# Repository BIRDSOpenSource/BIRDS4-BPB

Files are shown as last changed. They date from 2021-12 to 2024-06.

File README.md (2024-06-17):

<div align="center">
  <a href="https://lean-sat.org/opensource/">
  
  </a>
</div>

 

# BIRDS4-BPB
 Documentation for the Backplane Board used in the BIRDS4 Satellite

## About the BIRDS4 Program:

The Mission Statement of the Project is:

> “By successfully building and operating first satellite of nation, advance toward indigenous space program in each country”

The project is led by Kyushu Institute of Technology in Japan and involves students from Philippines, Paraguay, Nepal, Turkey and Japan.

Satellite Names: Tsuru (Japan), Guarani-1 (Paraguay) and Maya-2 (Phillipines)

Stakeholders:  Paraguayan Space Agency, Polytechnic Faculty of National University of Asuncion, and Kyushu Institute of Technology (Kyutech) for Japan.

Project duration: 2018-2022

CubeSat: 1U (10x10x10) cm3

Weight: 1.13kg

Launch Date: 21st February 2021 

BIRDS-4 has 1 main missions in total; APRS Store and forward mission

## Organisation structure

```bash

├── .gitattributes
├── B4_BPB_FM_PartsList_PBan_20191024.xls
├── BPB_v16.brd
├── BPB_v16.pdf
├── BPB_v16.sch
├── BPB_v16_BOT.png
├── BPB_v16_TOP.png
├── LICENSE
├── Photo.png
└── README.md

```

> [!CAUTION]
> The files `.sch` and `.brd` files in this repositiry were created using Eagle software.
 
For those that want to import these files into 
KiCAD7 [here's how you do it](https://community.element14.com/technologies/open-source-hardware/b/blog/posts/working-with-kicad-7-importing-eagle-files) 
 or KiCAD5.1 [here's how you do it](https://www.youtube.com/watch?v=RBc02MwpKxk&t=1s).
## Features

## I like this project, can I help you?
You are welcome 🙂

* Give us a star ⭐
* Watch repository to be notified about updates 👀
* If you will find some errors, report them in Issues 🐞
* Try Birds designs on some real computer and let us know how it worked in Discussions. 💬
* We would greatly appreciate if you would also tell others about this ecosystem, it helps us to improve BIRDS Open Source. Thank you!

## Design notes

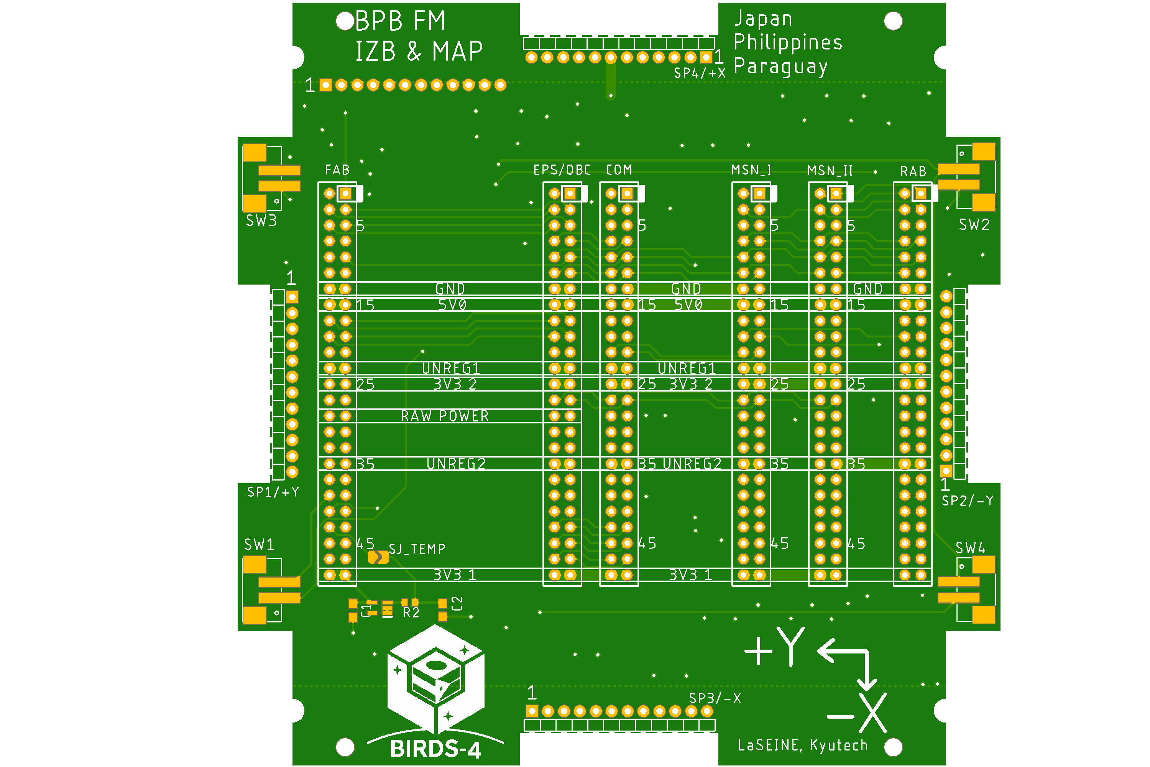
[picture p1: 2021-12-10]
BPB_v16_TOP.png

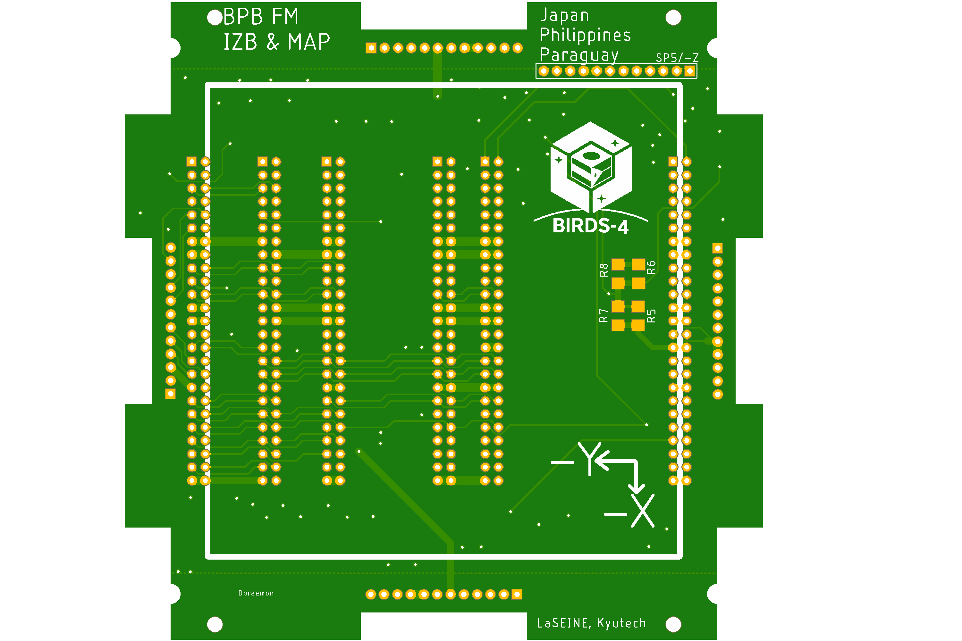
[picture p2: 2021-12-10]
BPB_v16_BOT.png

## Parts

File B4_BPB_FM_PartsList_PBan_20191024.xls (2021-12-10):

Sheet: 必ずお読みください
入力項目説明
メ ー カ ー |  |  | 電子部品のメーカー名をご入力ください。
部 品 種 別 |  |  | 電子部品の種別をご入力ください。例：チップ抵抗、トランジスタ、LED、など
電 子 部 品 型 番 |  |  | 電子部品の型番をご入力ください。 ※誤表記による不具合を回避するためにも正確なご入力をお願い致します。 ※表面実装の抵抗やコンデンサ(電解、タンタル以外)は、後述「電子部品見取り表」をご参照のうえ、ご入力ください。
配 置 記 号 / リファレンス |  |  | シルク図/配置図に表記された配置記号/リファレンス番号をご入力ください。 ※複数入力する場合は、カンマ「,」区切りでのご入力をお願い致します。 (入力例)R1～R5、R1-5と略さず、R1,R2,R3,R4,R5とご入力ください。 ※電子部品型番ベースでのご記入をお願い致します。（１つの電子部品型番に対して、配置番号を複数記入）
個 数 |  |  | 電子部品の個数をご入力ください。
ピ ン 数 |  |  | 電子部品の総ピン数をご入力ください。 ※基板取付穴、部品取付穴、全てのスルー・ノンスルーホール、面実装部品のパッド、及び次の①～⑤の配線を伴う箇所（①テストピン、②チェックランド、③引き出しランド、④ジャンパピン、⑤入出力ランドの総計。
実装 / 未実装 |  |  | 実装サービスでの「実装」/「未実装」をご選択ください。 ※同じ電子部品型番の中で実装と未実装が分かれる場合は、それぞれ2行に分けて配置記号をご入力ください。
部品分類 | SMD |  | 表面実装部品
 | DIP |  | 挿入部品
 | 特殊 BGA等 |  | BGA/CSP/LGA/QFNなど部品極性が部品の真下に配置された部品 -BGA：Ball Grid Array/下面に半田ボールの端子を配置したパッケージ。 -CSP：Chip Size Package/チッププサイズと同じか、もしくは僅かに大きいパッケージ。 -LGA：Land Grid Array/裏面に外部入出力用のランドを設けたパッケージ。※BGAの半田ボールがない。 -QFN：Quad Flat Non-Lead Package/QFPに似ていますが、外部入出力用のピンが出ていないパッケージ。
P板.com提供部品 (無料) |  |  | 【無償提供部品一覧】シートに記載されている「メーカー型番」を【部品リスト入力フォーム】シートのD列（電子部品型番）に入力し、I列（実装／未実装）を「実装」に設定いただくと、自動的に「○」が表示されます。 ※無料提供部品：チップコンデンサ/チップ抵抗を約1000種、実装サービスをご利用のお客様に無料提供いたします。 ※「○」が付かない場合は全半角の不一致などにより誤判定されている可能性があります。【無償提供部品一覧】シートより型番をコピー＆ペーストにて【部品リスト入力フォーム】にご入力ください。
 |  |  | http://www.p-ban.com/implementation/chip.html
P板.com調達部品(有料） |  |  | P板.com実装サービスで部品調達を希望される場合に○をご選択ください。 ※調達費用のお見積もりは、部品リストの返却と同時にご連絡いたします。 ※ご希望の納期や市場在庫状況によっては、調達が不可となる部品もございますので、予めご了承ください。
パッケージ情報 部品外形/部品仕様 |  |  | 電子部品のパッケージ情報をご入力ください。例：1608 , DIP , 0.5mmピッチQFP , 0.4mmピッチCN
コ メ ン ト |  |  | 特別なご指示のある電子部品について、自由にご入力ください。 例：未実装挿入穴のマスク処理が必要、など
版、変更履歴 |  |  | 部品種毎に、変更履歴を記載してください。 版は、アカウント登録の版に合わせて記載ください。
調達型式、代替型式 |  |  | 無料提供部品の在庫切れや、正確な調達型式を記載いたします。
部品名称見取り表
1.チップ部品（抵抗、コンデンサ）
 |  |  |  |  | 単位：ｍｍ
 |  |  | 電子部品型番 (C:コンデンサ、R:抵抗） | Ａ寸法 | Ｂ寸法
 |  |  | C/R1608 | 1.6 | 0.8
 |  |  | C/R2125 | 2 | 1.25
 |  |  | C/R3216 | 3.2 | 1.6
 |  |  | C/R3225 | 3.2 | 2.5
 |  |  | C/R4532 | 4.5 | 3.2
2.チップタンタルコンデンサ
 |  |  |  |  | 単位：ｍｍ
 |  |  | 電子部品型番 | Ａ寸法 | Ｂ寸法
 |  |  | CT3216 | 3.2 | 1.6
 |  |  | CT3528 | 3.5 | 2.8
 |  |  | CT4726 | 4.7 | 2.6
 |  |  | CT6032 | 6 | 3.2
 |  |  | CT5846 | 5.8 | 4.6
 |  |  | CT7343 | 7.3 | 4.3
3.チップアルミ電解コンデンサ
 |  |  |  |  |  | 単位：ｍｍ
 |  |  | 電子部品型番 | Ａ寸法 | Ｂ寸法 | C寸法
 |  |  | CE33 | 3.3 | 3.3 | φ3.0
 |  |  | CE43 | 4.3 | 4.3 | φ4.0
 |  |  | CE53 | 5.3 | 5.3 | φ5.0
 |  |  | CE66 | 6.6 | 6.6 | φ6.3
 |  |  | CE83 | 8.3 | 8.3 | φ8.0
 |  |  | CE103 | 10.3 | 10.3 | φ10.0
部品取り付け穴は、ピン数に含めてください。
コネクタの場合 |  |  |  |  |  | トランスの場合
部品リストフォーマット変更履歴
2014-02-01 | v2.0 | 松森 | 部品種別の総計を、直接関数に変更
 |  |  | ピン数合計、実装数合計数量を、直接関数に変更
 |  |  | 部品調達見積欄を修正
2014-03-11 | v2.1 | 松森 | *N列、O列が下の方、"○"選択リスト消えていたのを追加
 |  |  | *縮小しても解像度崩れず文字表示するため、フォントを"Meiryo UI"(Windows 標準添付)に変更
 |  |  | *136行目以降を非表示
 |  |  | *"X"列にリストを埋め込み
2014-06-12 | v2.2 | 松森 | *固定行を変更
 |  |  | *在庫状況列に条件付き書式設定
 |  |  | *その他各種バグ修正
2015-03-31 | V2.3 | 松森 | *無償提供部品を記載すると、無償提供部品欄に自動で"○"が表示されるよう条件式を挿入
 |  |  | *併せて、無償提供部品参照用一覧シートの作成・追加
 |  |  | *最小購入数が必要数量を下回る場合、セルを赤色にハッチングする
 |  |  | *シート1の名称変更
 |  |  | *変更履歴シートの追加
2015-06-19 | v2.4 | 松森 | ・ゼロΩ抵抗を無償対象に追加
 |  |  | ・変更履歴の列を追加し、変更履歴シートを削除
 |  |  | ・その他書式、印刷機能の変更
 |  |  | ・無償提供部品の入れ替え
2015-08-14 | v2.5 | 松森 | ・ゼロΩ抵抗の無償対象品が正しく反映されていなかったバグ修正
 |  |  | ・フォームへバージョン情報を埋め込み
2015-11-05 | v2.6 | 上田 | ・無償提供部品(RK73H2ATTD1601F)の抵抗値を正しい値に修正
2015-11-09 | v2.7 | 上田 | ・P板.com調達部品(無料)欄のフォントを変更
2016-01-15 | v2.8 | 箕浦 | ・無償提供部品一覧の「GRM32NF11E106Z」を削除
 |  |  | ・部品リスト入力フォームの4行目F列～L列の計算式が136行目以降を対象としていなかった不具合を修正
2016-01-27 | v2.9 | 箕浦 | ・「無償提供部品一覧」シートの表記修正
2016-08-26 | v2.10 | 松森 | ・「GRM31CF11E106Z」の許容差値修正
2016-11-15 | v2.11 | 松森 | ・部品調達欄表示順序変更
 |  |  | ・備考欄、荷姿欄追加
 |  |  | ・在庫状況のリスト微修正
2017-03-21 | v2.12 | 松森 | ・調達金額合計欄作成
 |  |  | ・在庫状況「長納期」を追加
 |  |  | ・その他微修正
2017-06-29 | v2.13 | 松森 | ・村田製3216サイズ以上のチップコンの取扱い中止
2017-07-19 | V2.14 | 松森 | ・KOA製1005サイズの定格電力を0.1Wに変更
 |  |  | (2015年10月のKOA仕様変更に伴う)
2017-09-14 | v2.15 | 松森 | ・KOA製2012サイズの定格電力を0.25Wへ変更
 |  |  | ・KOA製1608サイズ、1K以下の定格電力を0.125Wへ変更
 |  |  | ・MURATA製一部型式、許容差および定格修正
 |  |  | ・MURATA製一部部品削除
 |  |  | ・その他書式設定等微修正
2017-10-12 | v2.20 | 松森 | ・部品調達関連項目の移動
 |  |  | ・条件付き書式追加
2018-06-22 | v2.31 | 松森 | ・「1608」サイズと「2012」サイズのチップコンデンサを無償対象品から除外
2018-10-18 | V2.32 | 山田 | ・部品調達関連項目追加（条件付き書式追加/在庫状況：在庫少追加）
 |  |  | ・「必ずお読みください」シートの「配置記号 / リファレンス」の項目修正（配置記号の省略について）

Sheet: 部品リスト入力フォーム
Ver.2.32 |  |  | 電 子 部 品 型 番 ※半角英数字 ※サフィックスまで入力必須 | 配 置 記 号 リ フ ァ レ ン ス ※半角英数字） | 個数 | ピ ン 数 (部品取付穴 を含む） |  | 実装/ 未実装 | 部 品 分 類 |  |  | 必要数 実装枚数を入れてください。 ↓ | P板.com 提供 部品 (無料) | P板.com 調達 部品 (有料） | パッケージ情報 部品外形/部品仕様 | コ メ ン ト ※未実装挿入穴のマスク 処理が必要、など | 版 変更履歴 | 入荷数 | 返却
No | メーカー | 部品種別 |  |  |  | 1個 あたり | 合計 | 実装個数 | SMD | DIP | 特殊 BGA等 |  |  |  |  |  |  |  |  | P板.com部品調達使用欄
 |  |  |  |  | 19 | 87 | 385 | 19 | 8 | 11 | 0 | 6 | リスト (http://www.p-ban.com/implementation/chip.html)
例 | KOA | チップ抵抗 | RK73B2ATTD1002F | R1,R5,R9,R10 | 4 | 2 | 8 | 未実装 | SMD |  |  |  |  |  | 2012 |  | 4版 型式訂正、個数変更、 実装→未実装へ |  |  | 必要数 | 調達数 | 在庫状況 | メーカ | 調達品番 | 荷姿 | 納期 | 備考
1 □ | Hirosugi | 12 pin male pin header 90 | PSR-210154-12 | SP1/+Y SP2/-Y SP3/-X SP4/+X | 4 | 12 | 48 | 実装 | DIP |  |  | 24 |  |  | 12pin, H=1.5mm | place in component layer, solder in solder layer |  |  | □
2 □ | Hirosugi | 12 pin male pin header straight | PSS-210204-12 | SP5/-Z | 1 | 12 | 12 | 実装 | DIP |  |  | 6 |  |  | 12pin, H=2mm | place in solder layer, solder in component layer |  |  | □
3 □ | Hirose Electric Co Ltd | 50 pos female header | A3C-50DA-2DSA(71) | COM EPS/OBC FAB MSN_I MSN_II RAB | 6 | 50 | 300 | 実装 | DIP |  |  | 36 |  |  | 50 PIN, 2mm | place in component layer, solder in solder layer |  |  | □
4 □ | KOA | Resistor | RK73Z2BTTD | R6 R8 | 2 | 2 | 4 | 実装 | SMD |  |  | 12 | ○ |  | 3216 | place in solder layer, solder in solder layer |  |  | □
5 □ | Molex | Switch Connector | 554600272 | SW1 SW2 SW4 | 3 | 4 | 12 | 実装 | SMD |  |  | 18 |  |  | 2 ポジション ヘッダ コネクタ 0.079インチ（2.00mm） | place in component layer, solder in component layer |  |  | □
6 □ | Texas Instruments | Temperature Sensor | LMT84QDCKTQ1 | SJTEMP | 1 | 5 | 5 | 実装 | SMD |  |  | 6 |  |  | H=1.1 mm | place in component layer, solder in component layer |  |  | □
7 □ | TDK | Capacitor | C-USC0603 | C1, C2 | 2 | 2 | 4 | 実装 | SMD |  |  | 12 |  |  | 603 | place in component layer, solder in component layer |  |  | □
8 □ |  |  |  |  |  |  |  | 実装 |  |  |  | 0 |  |  |  |  |  |  | □
9 □ |  |  |  |  |  |  |  | 実装 |  |  |  | 0 |  |  |  |  |  |  | □
10 □ |  |  |  |  |  |  |  | 実装 |  |  |  | 0 |  |  |  |  |  |  | □
11 □ |  |  |  |  |  |  |  | 実装 |  |  |  | 0 |  |  |  |  |  |  | □
12 □ |  |  |  |  |  |  |  | 実装 |  |  |  | 0 |  |  |  |  |  |  | □
13 □ |  |  |  |  |  |  |  | 実装 |  |  |  | 0 |  |  |  |  |  |  | □
14 □ |  |  |  |  |  |  |  | 実装 |  |  |  | 0 |  |  |  |  |  |  | □
15 □ |  |  |  |  |  |  |  | 実装 |  |  |  | 0 |  |  |  |  |  |  | □
16 □ |  |  |  |  |  |  |  | 実装 |  |  |  | 0 |  |  |  |  |  |  | □
17 □ |  |  |  |  |  |  |  | 実装 |  |  |  | 0 |  |  |  |  |  |  | □
18 □ |  |  |  |  |  |  |  | 実装 |  |  |  | 0 |  |  |  |  |  |  | □
19 □ |  |  |  |  |  |  |  | 実装 |  |  |  | 0 |  |  |  |  |  |  | □
20 □ |  |  |  |  |  |  |  | 実装 |  |  |  | 0 |  |  |  |  |  |  | □
21 □ |  |  |  |  |  |  |  | 実装 |  |  |  | 0 |  |  |  |  |  |  | □
22 □ |  |  |  |  |  |  |  | 実装 |  |  |  | 0 |  |  |  |  |  |  | □
23 □ |  |  |  |  |  |  |  | 実装 |  |  |  | 0 |  |  |  |  |  |  | □
24 □ |  |  |  |  |  |  |  | 実装 |  |  |  | 0 |  |  |  |  |  |  | □
25 □ |  |  |  |  |  |  |  | 実装 |  |  |  | 0 |  |  |  |  |  |  | □
26 □ |  |  |  |  |  |  |  | 実装 |  |  |  | 0 |  |  |  |  |  |  | □
27 □ |  |  |  |  |  |  |  | 実装 |  |  |  | 0 |  |  |  |  |  |  | □
28 □ |  |  |  |  |  |  |  | 実装 |  |  |  | 0 |  |  |  |  |  |  | □
29 □ |  |  |  |  |  |  |  | 実装 |  |  |  | 0 |  |  |  |  |  |  | □
30 □ |  |  |  |  |  |  |  | 実装 |  |  |  | 0 |  |  |  |  |  |  | □
31 □ |  |  |  |  |  |  |  | 実装 |  |  |  | 0 |  |  |  |  |  |  | □
32 □ |  |  |  |  |  |  |  | 実装 |  |  |  | 0 |  |  |  |  |  |  | □
33 □ |  |  |  |  |  |  |  | 実装 |  |  |  | 0 |  |  |  |  |  |  | □
34 □ |  |  |  |  |  |  |  | 実装 |  |  |  | 0 |  |  |  |  |  |  | □
35 □ |  |  |  |  |  |  |  | 実装 |  |  |  | 0 |  |  |  |  |  |  | □
36 □ |  |  |  |  |  |  |  | 実装 |  |  |  | 0 |  |  |  |  |  |  | □
37 □ |  |  |  |  |  |  |  | 実装 |  |  |  | 0 |  |  |  |  |  |  | □
38 □ |  |  |  |  |  |  |  | 実装 |  |  |  | 0 |  |  |  |  |  |  | □
39 □ |  |  |  |  |  |  |  | 実装 |  |  |  | 0 |  |  |  |  |  |  | □
40 □ |  |  |  |  |  |  |  | 未実装 |  |  |  | 0 |  |  |  |  |  |  | □
41 □ |  |  |  |  |  |  |  | 未実装 |  |  |  | 0 |  |  |  |  |  |  | □
42 □ |  |  |  |  |  |  |  | 未実装 |  |  |  | 0 |  |  |  |  |  |  | □
43 □ |  |  |  |  |  |  |  | 未実装 |  |  |  | 0 |  |  |  |  |  |  | □
44 □ |  |  |  |  |  |  |  | 未実装 |  |  |  | 0 |  |  |  |  |  |  | □
45 □ |  |  |  |  |  |  |  | 実装 |  |  |  | 0 |  |  |  |  |  |  | □
46 □ |  |  |  |  |  |  |  |  |  |  |  |  |  |  |  |  |  |  | □
47 □ |  |  |  |  |  |  |  |  |  |  |  |  |  |  |  |  |  |  | □
48 □ |  |  |  |  |  |  |  |  |  |  |  |  |  |  |  |  |  |  | □
49 □ |  |  |  |  |  |  |  |  |  |  |  |  |  |  |  |  |  |  | □
50 □ |  |  |  |  |  |  |  |  |  |  |  |  |  |  |  |  |  |  | □
51 □ |  |  |  |  |  |  |  |  |  |  |  |  |  |  |  |  |  |  | □
52 □ |  |  |  |  |  |  |  |  |  |  |  |  |  |  |  |  |  |  | □
53 □ |  |  |  |  |  |  |  |  |  |  |  |  |  |  |  |  |  |  | □
54 □ |  |  |  |  |  |  |  |  |  |  |  |  |  |  |  |  |  |  | □
55 □ |  |  |  |  |  |  |  |  |  |  |  |  |  |  |  |  |  |  | □
56 □ |  |  |  |  |  |  |  |  |  |  |  |  |  |  |  |  |  |  | □
57 □ |  |  |  |  |  |  |  |  |  |  |  |  |  |  |  |  |  |  | □
58 □ |  |  |  |  |  |  |  |  |  |  |  |  |  |  |  |  |  |  | □
59 □ |  |  |  |  |  |  |  |  |  |  |  |  |  |  |  |  |  |  | □
60 □ |  |  |  |  |  |  |  |  |  |  |  |  |  |  |  |  |  |  | □
61 □ |  |  |  |  |  |  |  |  |  |  |  |  |  |  |  |  |  |  | □
62 □ |  |  |  |  |  |  |  |  |  |  |  |  |  |  |  |  |  |  | □
63 □ |  |  |  |  |  |  |  |  |  |  |  |  |  |  |  |  |  |  | □
64 □ |  |  |  |  |  |  |  |  |  |  |  |  |  |  |  |  |  |  | □
65 □ |  |  |  |  |  |  |  |  |  |  |  |  |  |  |  |  |  |  | □
66 □ |  |  |  |  |  |  |  |  |  |  |  |  |  |  |  |  |  |  | □
67 □ |  |  |  |  |  |  |  |  |  |  |  |  |  |  |  |  |  |  | □
68 □ |  |  |  |  |  |  |  |  |  |  |  |  |  |  |  |  |  |  | □
69 □ |  |  |  |  |  |  |  |  |  |  |  |  |  |  |  |  |  |  | □
70 □ |  |  |  |  |  |  |  |  |  |  |  |  |  |  |  |  |  |  | □
71 □ |  |  |  |  |  |  |  |  |  |  |  |  |  |  |  |  |  |  | □
72 □ |  |  |  |  |  |  |  |  |  |  |  |  |  |  |  |  |  |  | □
73 □ |  |  |  |  |  |  |  |  |  |  |  |  |  |  |  |  |  |  | □
74 □ |  |  |  |  |  |  |  |  |  |  |  |  |  |  |  |  |  |  | □
75 □ |  |  |  |  |  |  |  |  |  |  |  |  |  |  |  |  |  |  | □
76 □ |  |  |  |  |  |  |  |  |  |  |  |  |  |  |  |  |  |  | □
77 □ |  |  |  |  |  |  |  |  |  |  |  |  |  |  |  |  |  |  | □
78 □ |  |  |  |  |  |  |  |  |  |  |  |  |  |  |  |  |  |  | □
79 □ |  |  |  |  |  |  |  |  |  |  |  |  |  |  |  |  |  |  | □
80 □ |  |  |  |  |  |  |  |  |  |  |  |  |  |  |  |  |  |  | □
81 □ |  |  |  |  |  |  |  |  |  |  |  |  |  |  |  |  |  |  | □
82 □ |  |  |  |  |  |  |  |  |  |  |  |  |  |  |  |  |  |  | □
83 □ |  |  |  |  |  |  |  |  |  |  |  |  |  |  |  |  |  |  | □
84 □ |  |  |  |  |  |  |  |  |  |  |  |  |  |  |  |  |  |  | □
85 □ |  |  |  |  |  |  |  |  |  |  |  |  |  |  |  |  |  |  | □
86 □ |  |  |  |  |  |  |  |  |  |  |  |  |  |  |  |  |  |  | □
87 □ |  |  |  |  |  |  |  |  |  |  |  |  |  |  |  |  |  |  | □
88 □ |  |  |  |  |  |  |  |  |  |  |  |  |  |  |  |  |  |  | □
89 □ |  |  |  |  |  |  |  |  |  |  |  |  |  |  |  |  |  |  | □
90 □ |  |  |  |  |  |  |  |  |  |  |  |  |  |  |  |  |  |  | □
91 □ |  |  |  |  |  |  |  |  |  |  |  |  |  |  |  |  |  |  | □
92 □ |  |  |  |  |  |  |  |  |  |  |  |  |  |  |  |  |  |  | □
93 □ |  |  |  |  |  |  |  |  |  |  |  |  |  |  |  |  |  |  | □
94 □ |  |  |  |  |  |  |  |  |  |  |  |  |  |  |  |  |  |  | □
95 □ |  |  |  |  |  |  |  |  |  |  |  |  |  |  |  |  |  |  | □
96 □ |  |  |  |  |  |  |  |  |  |  |  |  |  |  |  |  |  |  | □
97 □ |  |  |  |  |  |  |  |  |  |  |  |  |  |  |  |  |  |  | □
98 □ |  |  |  |  |  |  |  |  |  |  |  |  |  |  |  |  |  |  | □
99 □ |  |  |  |  |  |  |  |  |  |  |  |  |  |  |  |  |  |  | □
100 □ |  |  |  |  |  |  |  |  |  |  |  |  |  |  |  |  |  |  | □
101 □ |  |  |  |  |  |  |  |  |  |  |  |  |  |  |  |  |  |  | □
102 □ |  |  |  |  |  |  |  |  |  |  |  |  |  |  |  |  |  |  | □
103 □ |  |  |  |  |  |  |  |  |  |  |  |  |  |  |  |  |  |  | □
104 □ |  |  |  |  |  |  |  |  |  |  |  |  |  |  |  |  |  |  | □
105 □ |  |  |  |  |  |  |  |  |  |  |  |  |  |  |  |  |  |  | □
106 □ |  |  |  |  |  |  |  |  |  |  |  |  |  |  |  |  |  |  | □
107 □ |  |  |  |  |  |  |  |  |  |  |  |  |  |  |  |  |  |  | □
108 □ |  |  |  |  |  |  |  |  |  |  |  |  |  |  |  |  |  |  | □
109 □ |  |  |  |  |  |  |  |  |  |  |  |  |  |  |  |  |  |  | □
110 □ |  |  |  |  |  |  |  |  |  |  |  |  |  |  |  |  |  |  | □
111 □ |  |  |  |  |  |  |  |  |  |  |  |  |  |  |  |  |  |  | □
112 □ |  |  |  |  |  |  |  |  |  |  |  |  |  |  |  |  |  |  | □
113 □ |  |  |  |  |  |  |  |  |  |  |  |  |  |  |  |  |  |  | □
114 □ |  |  |  |  |  |  |  |  |  |  |  |  |  |  |  |  |  |  | □
115 □ |  |  |  |  |  |  |  |  |  |  |  |  |  |  |  |  |  |  | □
116 □ |  |  |  |  |  |  |  |  |  |  |  |  |  |  |  |  |  |  | □
117 □ |  |  |  |  |  |  |  |  |  |  |  |  |  |  |  |  |  |  | □
118 □ |  |  |  |  |  |  |  |  |  |  |  |  |  |  |  |  |  |  | □
119 □ |  |  |  |  |  |  |  |  |  |  |  |  |  |  |  |  |  |  | □
120 □ |  |  |  |  |  |  |  |  |  |  |  |  |  |  |  |  |  |  | □
121 □ |  |  |  |  |  |  |  |  |  |  |  |  |  |  |  |  |  |  | □
122 □ |  |  |  |  |  |  |  |  |  |  |  |  |  |  |  |  |  |  | □
123 □ |  |  |  |  |  |  |  |  |  |  |  |  |  |  |  |  |  |  | □
124 □ |  |  |  |  |  |  |  |  |  |  |  |  |  |  |  |  |  |  | □
125 □ |  |  |  |  |  |  |  |  |  |  |  |  |  |  |  |  |  |  | □
126 □ |  |  |  |  |  |  |  |  |  |  |  |  |  |  |  |  |  |  | □
127 □ |  |  |  |  |  |  |  |  |  |  |  |  |  |  |  |  |  |  | □
128 □ |  |  |  |  |  |  |  |  |  |  |  |  |  |  |  |  |  |  | □
129 □ |  |  |  |  |  |  |  |  |  |  |  |  |  |  |  |  |  |  | □
130 □ |  |  |  |  |  |  |  |  |  |  |  |  |  |  |  |  |  |  | □
131 □ |  |  |  |  |  |  |  |  |  |  |  |  |  |  |  |  |  |  | □
132 □ |  |  |  |  |  |  |  |  |  |  |  |  |  |  |  |  |  |  | □
133 □ |  |  |  |  |  |  |  |  |  |  |  |  |  |  |  |  |  |  | □
134 □ |  |  |  |  |  |  |  |  |  |  |  |  |  |  |  |  |  |  | □
135 □ |  |  |  |  |  |  |  |  |  |  |  |  |  |  |  |  |  |  | □
136 □ |  |  |  |  |  |  |  |  |  |  |  |  |  |  |  |  |  |  | □
137 □ |  |  |  |  |  |  |  |  |  |  |  |  |  |  |  |  |  |  | □
138 □ |  |  |  |  |  |  |  |  |  |  |  |  |  |  |  |  |  |  | □
139 □ |  |  |  |  |  |  |  |  |  |  |  |  |  |  |  |  |  |  | □
140 □ |  |  |  |  |  |  |  |  |  |  |  |  |  |  |  |  |  |  | □
141 □ |  |  |  |  |  |  |  |  |  |  |  |  |  |  |  |  |  |  | □
142 □ |  |  |  |  |  |  |  |  |  |  |  |  |  |  |  |  |  |  | □
143 □ |  |  |  |  |  |  |  |  |  |  |  |  |  |  |  |  |  |  | □
144 □ |  |  |  |  |  |  |  |  |  |  |  |  |  |  |  |  |  |  | □
145 □ |  |  |  |  |  |  |  |  |  |  |  |  |  |  |  |  |  |  | □
146 □ |  |  |  |  |  |  |  |  |  |  |  |  |  |  |  |  |  |  | □
147 □ |  |  |  |  |  |  |  |  |  |  |  |  |  |  |  |  |  |  | □
148 □ |  |  |  |  |  |  |  |  |  |  |  |  |  |  |  |  |  |  | □
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

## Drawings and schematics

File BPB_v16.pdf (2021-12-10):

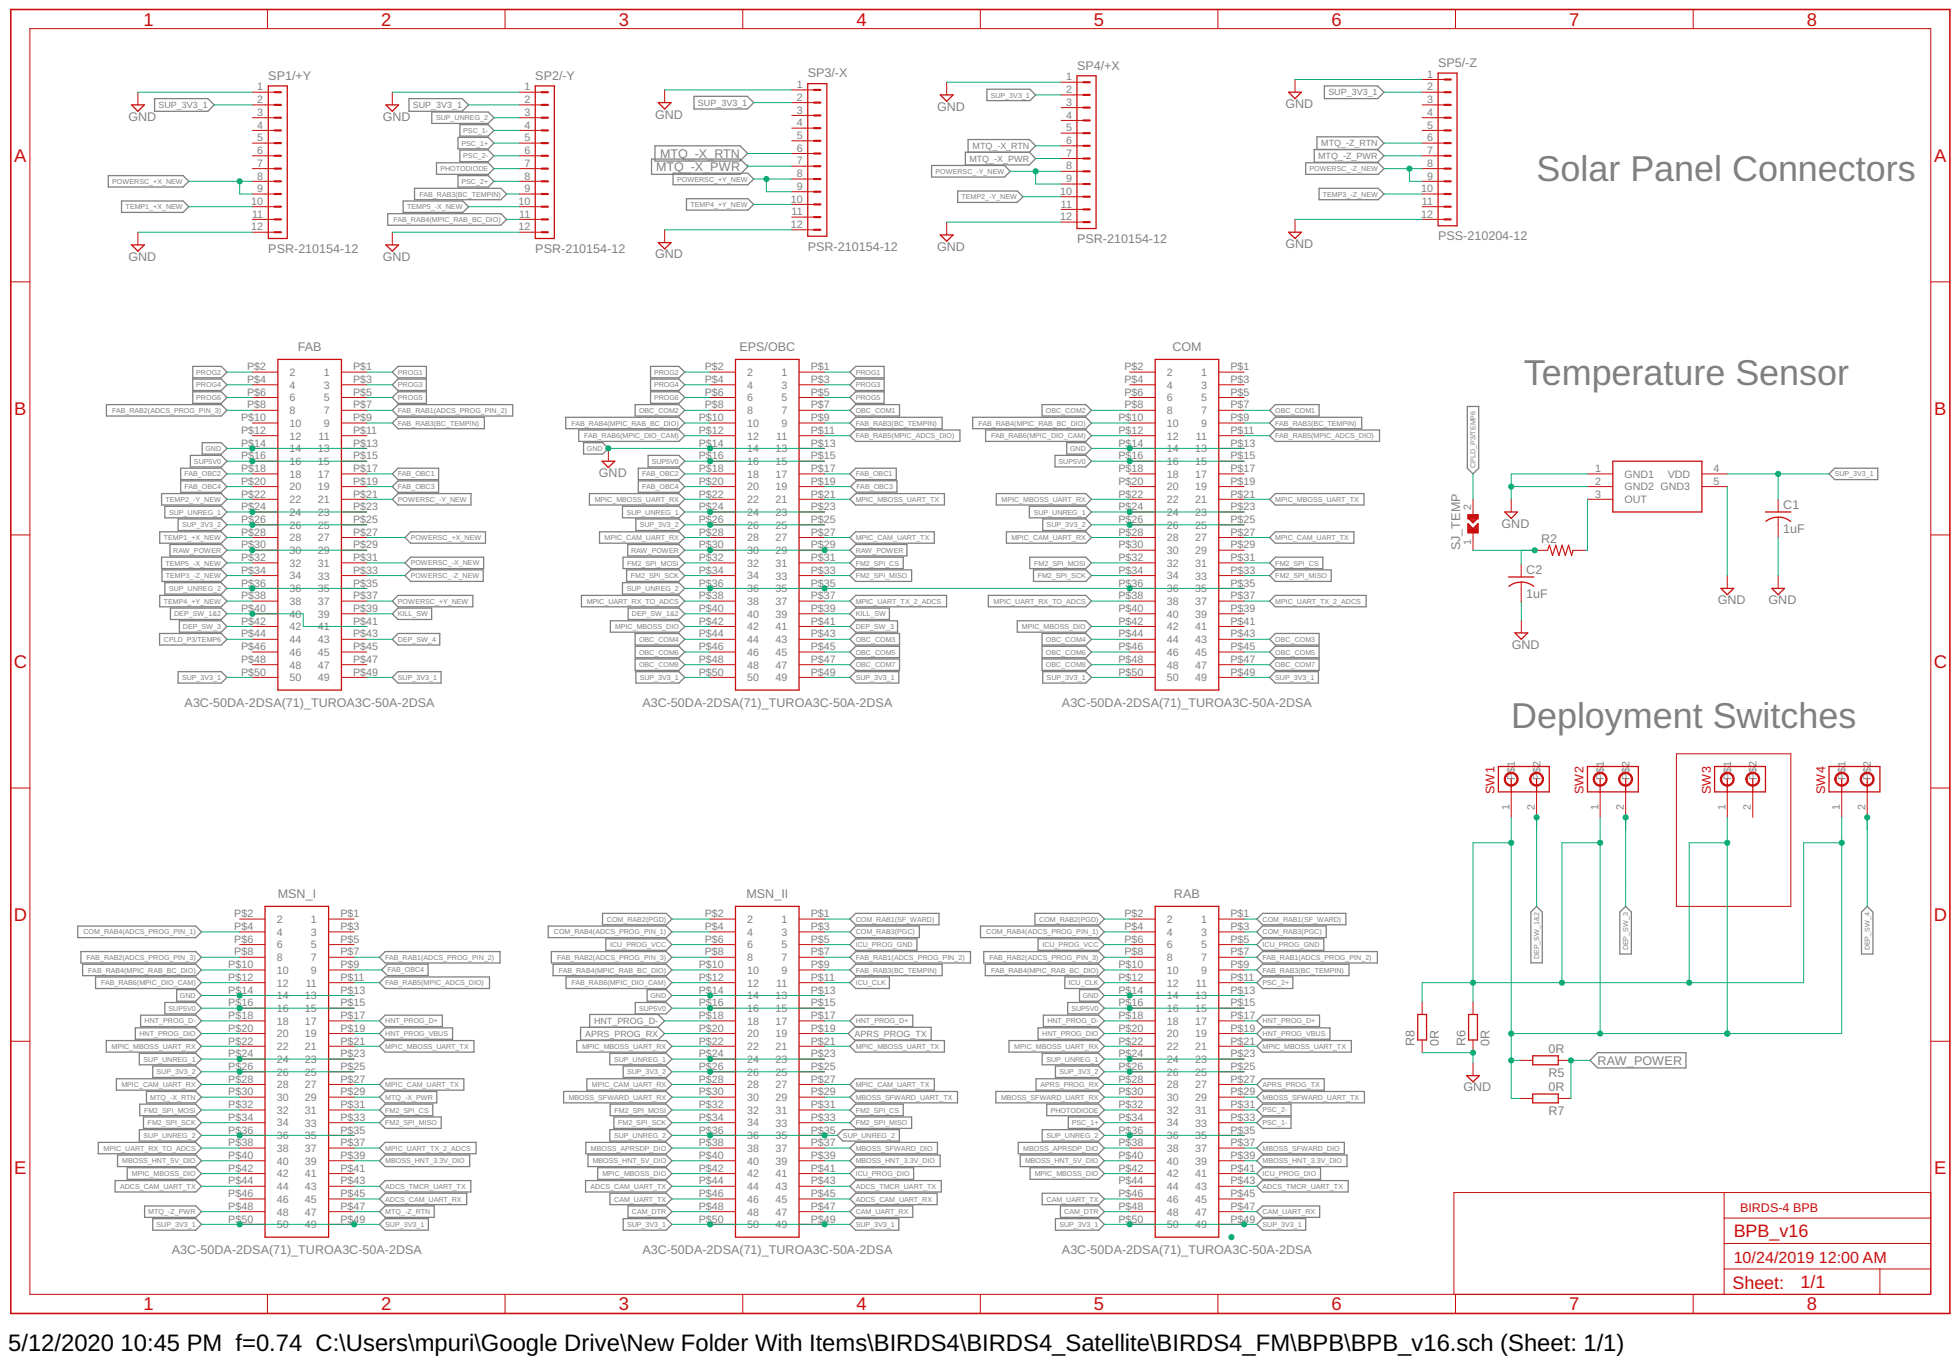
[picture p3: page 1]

5/12/2020 10:45 PM f=0.74 C:\Users\mpuri\Google Drive\New Folder With Items\BIRDS4\BIRDS4_Satellite\BIRDS4_FM\BPB\BPB_v16.sch (Sheet: 1/1)

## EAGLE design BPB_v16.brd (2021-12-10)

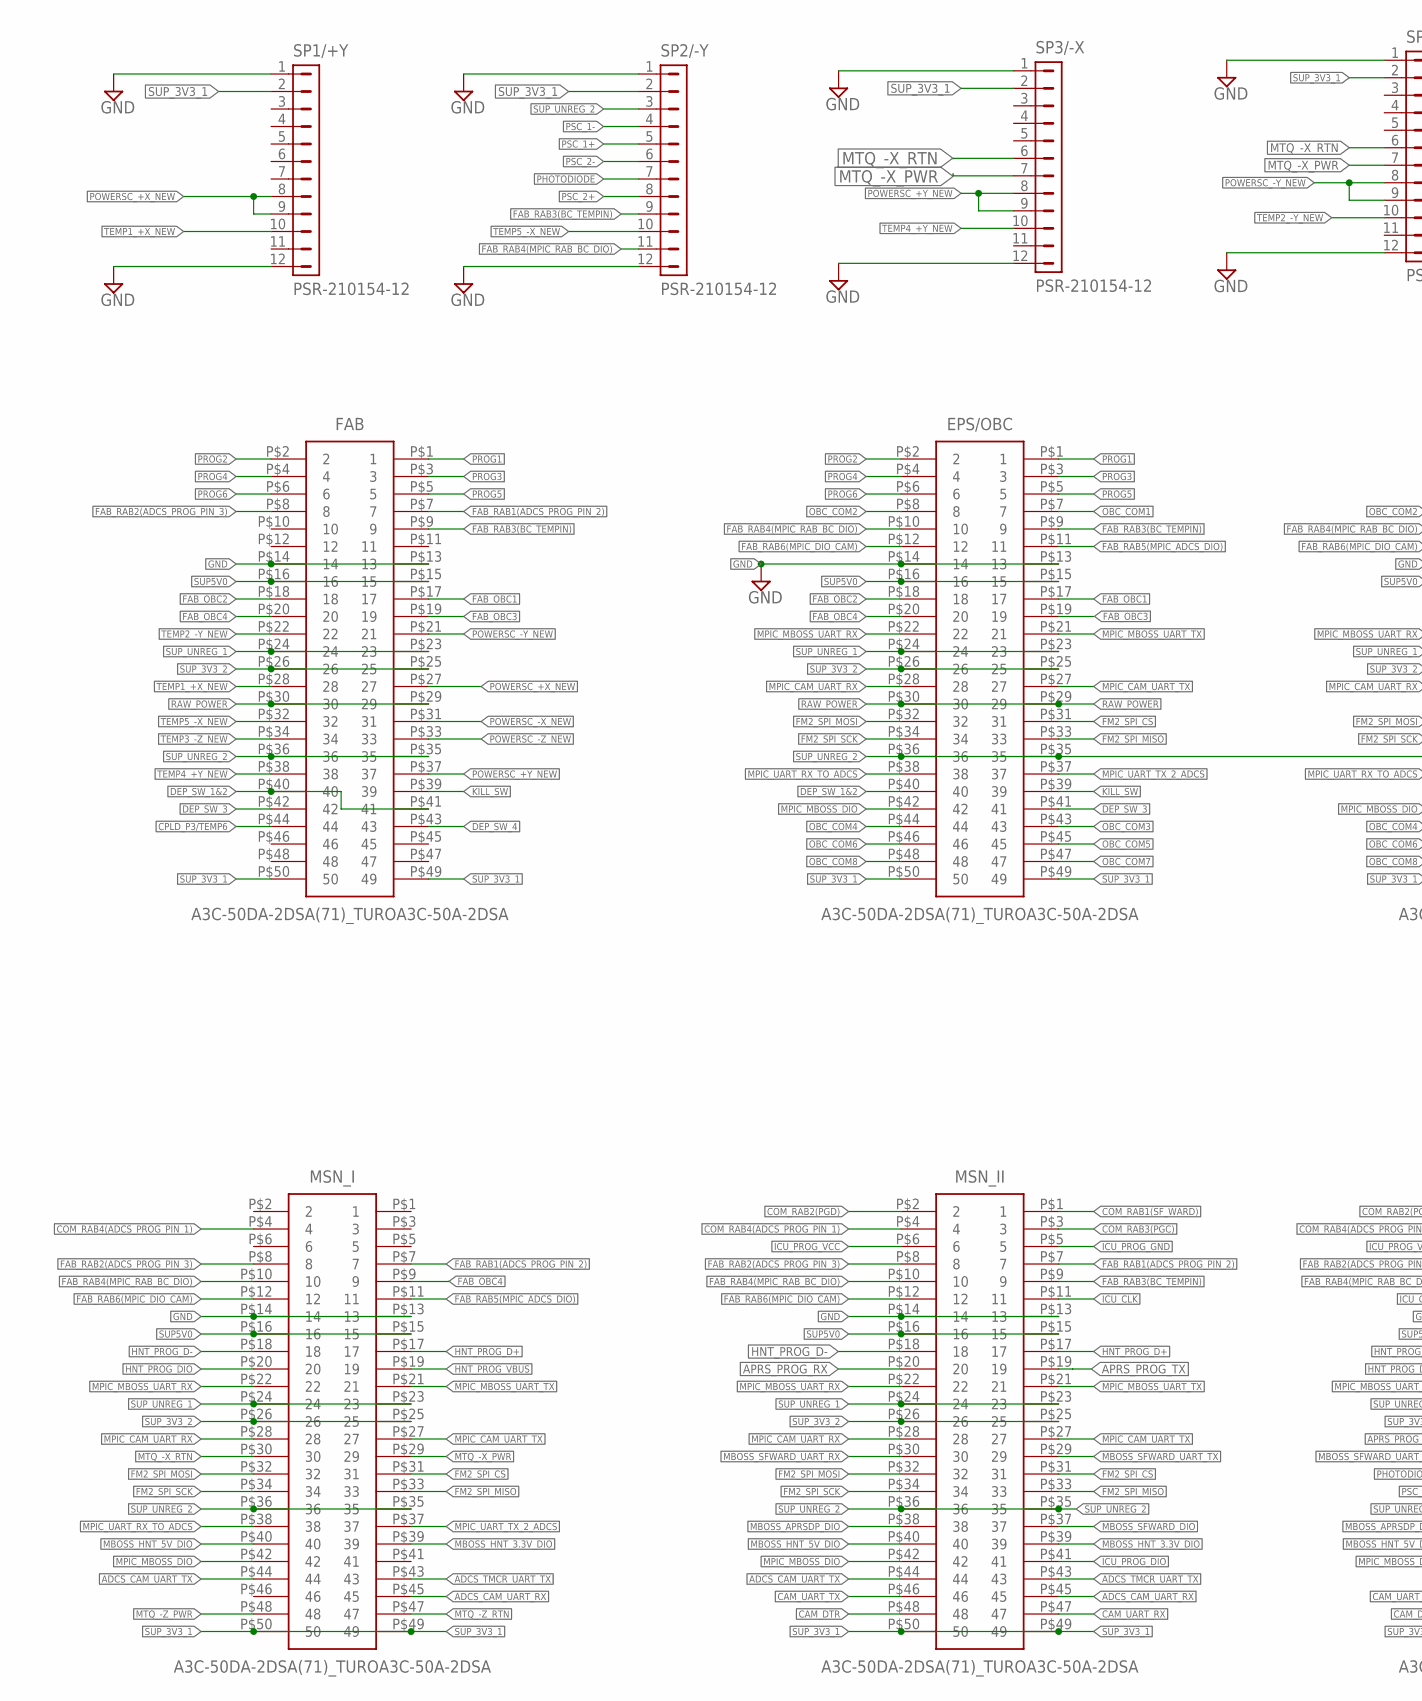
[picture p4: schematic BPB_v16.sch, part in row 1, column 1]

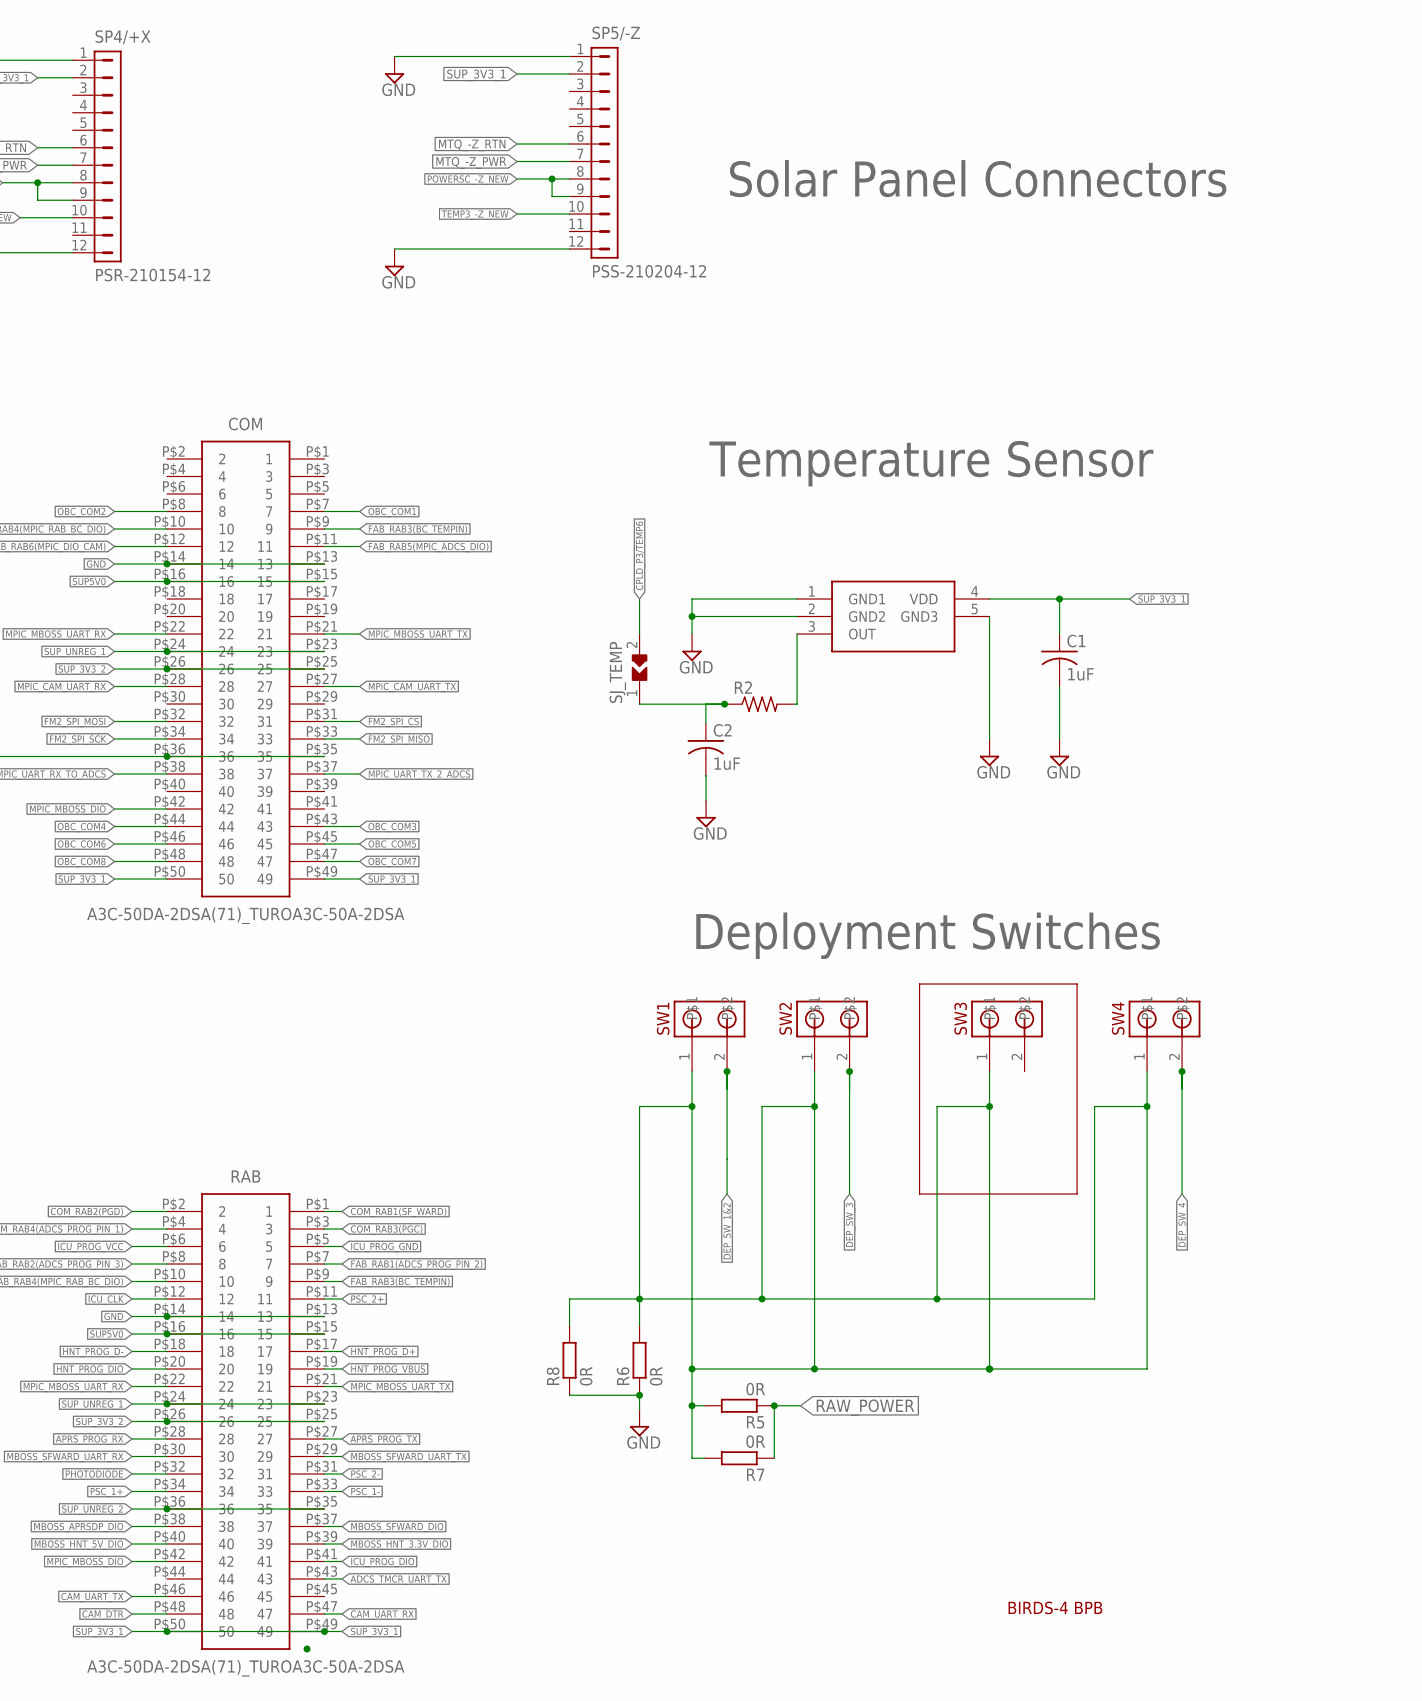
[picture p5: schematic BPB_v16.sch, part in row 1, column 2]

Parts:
C1, C2: 1uF; C0603
COM: A3C-50DA-2DSA(71)_TUROA3C-50A-2DSA; SHDR50W60P200_2X25_5000X400X44_TR
EPS/OBC: A3C-50DA-2DSA(71)_TUROA3C-50A-2DSA; SHDR50W60P200_2X25_5000X400X44_TR
FAB: A3C-50DA-2DSA(71)_TUROA3C-50A-2DSA; SHDR50W60P200_2X25_5000X400X44_TR
MSN_I: A3C-50DA-2DSA(71)_TUROA3C-50A-2DSA; SHDR50W60P200_2X25_5000X400X44_TR
MSN_II: A3C-50DA-2DSA(71)_TUROA3C-50A-2DSA; SHDR50W60P200_2X25_5000X400X44_TR
R2: R-US_R0402; R0402
R5, R6, R7, R8: 0R; R3216
RAB: A3C-50DA-2DSA(71)_TUROA3C-50A-2DSA; SHDR50W60P200_2X25_5000X400X44_TR
SJ_TEMP: SJ_BY_TURO; SJ_TURO
SP1/+Y, SP2/-Y, SP3/-X, SP4/+X: PSR-210154-12; PIN1X12/90
SP5/-Z: PSS-210204-12; PIN1X12
SW1, SW2, SW3, SW4: MOLEX-CONN-2-0554600272; MOLEX-CONN-2-BIRDS
U$3: LMT84DCKT; SOT65P210X110-5N

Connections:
ADCS_CAM_UART_RX: MSN_I.P$45 (45), MSN_II.P$45 (45)
ADCS_CAM_UART_TX: MSN_I.P$44 (44), MSN_II.P$44 (44)
ADCS_TMCR_UART_TX: MSN_I.P$43 (43), MSN_II.P$43 (43), RAB.P$43 (43)
APRS_PROG_RX: MSN_II.P$20 (20), RAB.P$28 (28)
APRS_PROG_TX: MSN_II.P$19 (19), RAB.P$27 (27)
CAM_DTR: MSN_II.P$48 (48), RAB.P$48 (48)
CAM_UART_RX: MSN_II.P$47 (47), RAB.P$47 (47)
CAM_UART_TX: MSN_II.P$46 (46), RAB.P$46 (46)
COM_RAB1(SF_WARD): MSN_II.P$1 (1), RAB.P$1 (1)
COM_RAB2(PGD): MSN_II.P$2 (2), RAB.P$2 (2)
COM_RAB3(PGC): MSN_II.P$3 (3), RAB.P$3 (3)
COM_RAB4(ADCS_PROG_PIN_1): MSN_I.P$4 (4), MSN_II.P$4 (4), RAB.P$4 (4)
CPLD_P3/TEMP6: FAB.P$44 (44), SJ_TEMP.2
DEP_SW_1&2: EPS/OBC.P$40 (40), FAB.P$40 (40), FAB.P$41 (41), SW1.2
DEP_SW_3: EPS/OBC.P$41 (41), FAB.P$42 (42), SW2.2
DEP_SW_4: FAB.P$43 (43), SW4.2
DEP_SW_POWER: R5.2, R6.2, R7.2, R8.2, SW1.1, SW2.1, SW3.1, SW4.1
FAB_OBC1: EPS/OBC.P$17 (17), FAB.P$17 (17)
FAB_OBC2: EPS/OBC.P$18 (18), FAB.P$18 (18)
FAB_OBC3: EPS/OBC.P$19 (19), FAB.P$19 (19)
FAB_OBC4: EPS/OBC.P$20 (20), FAB.P$20 (20), MSN_I.P$9 (9)
FAB_RAB1(ADCS_PROG_PIN_2): FAB.P$7 (7), MSN_I.P$7 (7), MSN_II.P$7 (7), RAB.P$7 (7)
FAB_RAB2(ADCS_PROG_PIN_3): FAB.P$8 (8), MSN_I.P$8 (8), MSN_II.P$8 (8), RAB.P$8 (8)
FAB_RAB3(BC_TEMPIN): COM.P$9 (9), EPS/OBC.P$9 (9), FAB.P$9 (9), MSN_II.P$9 (9), RAB.P$9 (9), SP2/-Y.9
FAB_RAB4(MPIC_RAB_BC_DIO): COM.P$10 (10), EPS/OBC.P$10 (10), MSN_I.P$10 (10), MSN_II.P$10 (10), RAB.P$10 (10), SP2/-Y.11
FAB_RAB5(MPIC_ADCS_DIO): COM.P$11 (11), EPS/OBC.P$11 (11), MSN_I.P$11 (11)
FAB_RAB6(MPIC_DIO_CAM): COM.P$12 (12), EPS/OBC.P$12 (12), MSN_I.P$12 (12), MSN_II.P$12 (12)
FM2_SPI_CS: COM.P$31 (31), EPS/OBC.P$31 (31), MSN_I.P$31 (31), MSN_II.P$31 (31)
FM2_SPI_MISO: COM.P$33 (33), EPS/OBC.P$33 (33), MSN_I.P$33 (33), MSN_II.P$33 (33)
FM2_SPI_MOSI: COM.P$32 (32), EPS/OBC.P$32 (32), MSN_I.P$32 (32), MSN_II.P$32 (32)
FM2_SPI_SCK: COM.P$34 (34), EPS/OBC.P$34 (34), MSN_I.P$34 (34), MSN_II.P$34 (34)
GND: C1.2, C2.2, COM.P$13 (13), COM.P$14 (14), EPS/OBC.P$13 (13), EPS/OBC.P$14 (14), FAB.P$13 (13), FAB.P$14 (14), MSN_I.P$13 (13), MSN_I.P$14 (14), MSN_II.P$13 (13), MSN_II.P$14 (14), R6.1, R8.1, RAB.P$13 (13), RAB.P$14 (14), SP1/+Y.1, SP1/+Y.12, SP2/-Y.1, SP2/-Y.12, SP3/-X.1, SP3/-X.12, SP4/+X.1, SP4/+X.12, SP5/-Z.1, SP5/-Z.12, U$3.1 (GND1), U$3.2 (GND2), U$3.5 (GND3)
HNT_PROG_D+: MSN_I.P$17 (17), MSN_II.P$17 (17), RAB.P$17 (17)
HNT_PROG_D-: MSN_I.P$18 (18), MSN_II.P$18 (18), RAB.P$18 (18)
HNT_PROG_DIO: MSN_I.P$20 (20), RAB.P$20 (20)
HNT_PROG_VBUS: MSN_I.P$19 (19), RAB.P$19 (19)
ICU_CLK: MSN_II.P$11 (11), RAB.P$12 (12)
ICU_PROG_DIO: MSN_II.P$41 (41), RAB.P$41 (41)
ICU_PROG_GND: MSN_II.P$5 (5), RAB.P$5 (5)
ICU_PROG_VCC: MSN_II.P$6 (6), RAB.P$6 (6)
KILL_SW: EPS/OBC.P$39 (39), FAB.P$39 (39)
MBOSS_APRSDP_DIO: MSN_II.P$38 (38), RAB.P$38 (38)
MBOSS_HNT_3.3V_DIO: MSN_I.P$39 (39), MSN_II.P$39 (39), RAB.P$39 (39)
MBOSS_HNT_5V_DIO: MSN_I.P$40 (40), MSN_II.P$40 (40), RAB.P$40 (40)
MBOSS_SFWARD_DIO: MSN_II.P$37 (37), RAB.P$37 (37)
MBOSS_SFWARD_UART_RX: MSN_II.P$30 (30), RAB.P$30 (30)
MBOSS_SFWARD_UART_TX: MSN_II.P$29 (29), RAB.P$29 (29)
MPIC_CAM_UART_RX: COM.P$28 (28), EPS/OBC.P$28 (28), MSN_I.P$28 (28), MSN_II.P$28 (28)
MPIC_CAM_UART_TX: COM.P$27 (27), EPS/OBC.P$27 (27), MSN_I.P$27 (27), MSN_II.P$27 (27)
MPIC_MBOSS_DIO: COM.P$42 (42), EPS/OBC.P$42 (42), MSN_I.P$42 (42), MSN_II.P$42 (42), RAB.P$42 (42)
MPIC_MBOSS_UART_RX: COM.P$22 (22), EPS/OBC.P$22 (22), MSN_I.P$22 (22), MSN_II.P$22 (22), RAB.P$22 (22)
MPIC_MBOSS_UART_TX: COM.P$21 (21), EPS/OBC.P$21 (21), MSN_I.P$21 (21), MSN_II.P$21 (21), RAB.P$21 (21)
MPIC_UART_RX_TO_ADCS: COM.P$38 (38), EPS/OBC.P$38 (38), MSN_I.P$38 (38)
MPIC_UART_TX_2_ADCS: COM.P$37 (37), EPS/OBC.P$37 (37), MSN_I.P$37 (37)
MTQ_-X_PWR: MSN_I.P$29 (29), SP3/-X.7, SP4/+X.7
MTQ_-X_RTN: MSN_I.P$30 (30), SP3/-X.6, SP4/+X.6
MTQ_-Z_PWR: MSN_I.P$48 (48), SP5/-Z.7
MTQ_-Z_RTN: MSN_I.P$47 (47), SP5/-Z.6
unnamed: C2.1, R2.1, SJ_TEMP.1
unnamed: R2.2, U$3.3 (OUT)
OBC_COM1: COM.P$7 (7), EPS/OBC.P$7 (7)
OBC_COM2: COM.P$8 (8), EPS/OBC.P$8 (8)
OBC_COM3: COM.P$43 (43), EPS/OBC.P$43 (43)
OBC_COM4: COM.P$44 (44), EPS/OBC.P$44 (44)
OBC_COM5: COM.P$45 (45), EPS/OBC.P$45 (45)
OBC_COM6: COM.P$46 (46), EPS/OBC.P$46 (46)
OBC_COM7: COM.P$47 (47), EPS/OBC.P$47 (47)
OBC_COM8: COM.P$48 (48), EPS/OBC.P$48 (48)
PHOTODIODE: RAB.P$32 (32), SP2/-Y.7
POWERSC_+X_NEW: FAB.P$27 (27), SP1/+Y.8, SP1/+Y.9
POWERSC_+Y_NEW: FAB.P$37 (37), SP3/-X.8, SP3/-X.9
POWERSC_-X_NEW: FAB.P$31 (31)
POWERSC_-Y_NEW: FAB.P$21 (21), SP4/+X.8, SP4/+X.9
POWERSC_-Z_NEW: FAB.P$33 (33), SP5/-Z.8, SP5/-Z.9
PROG1: EPS/OBC.P$1 (1), FAB.P$1 (1)
PROG2: EPS/OBC.P$2 (2), FAB.P$2 (2)
PROG3: EPS/OBC.P$3 (3), FAB.P$3 (3)
PROG4: EPS/OBC.P$4 (4), FAB.P$4 (4)
PROG5: EPS/OBC.P$5 (5), FAB.P$5 (5)
PROG6: EPS/OBC.P$6 (6), FAB.P$6 (6)
PSC_1+: RAB.P$34 (34), SP2/-Y.5
PSC_1-: RAB.P$33 (33), SP2/-Y.4
PSC_2+: RAB.P$11 (11), SP2/-Y.8
PSC_2-: RAB.P$31 (31), SP2/-Y.6
RAW_POWER: EPS/OBC.P$29 (29), EPS/OBC.P$30 (30), FAB.P$29 (29), FAB.P$30 (30), R5.1, R7.1
SUP5V0: COM.P$15 (15), COM.P$16 (16), EPS/OBC.P$15 (15), EPS/OBC.P$16 (16), FAB.P$15 (15), FAB.P$16 (16), MSN_I.P$15 (15), MSN_I.P$16 (16), MSN_II.P$15 (15), MSN_II.P$16 (16), RAB.P$15 (15), RAB.P$16 (16)
SUP_3V3_1: C1.1, COM.P$49 (49), COM.P$50 (50), EPS/OBC.P$49 (49), EPS/OBC.P$50 (50), FAB.P$49 (49), FAB.P$50 (50), MSN_I.P$49 (49), MSN_I.P$50 (50), MSN_II.P$49 (49), MSN_II.P$50 (50), RAB.P$49 (49), RAB.P$50 (50), SP1/+Y.2, SP2/-Y.2, SP3/-X.2, SP4/+X.2, SP5/-Z.2, U$3.4 (VDD)
SUP_3V3_2: COM.P$25 (25), COM.P$26 (26), EPS/OBC.P$25 (25), EPS/OBC.P$26 (26), FAB.P$25 (25), FAB.P$26 (26), MSN_I.P$25 (25), MSN_I.P$26 (26), MSN_II.P$25 (25), MSN_II.P$26 (26), RAB.P$25 (25), RAB.P$26 (26)
SUP_UNREG_1: COM.P$23 (23), COM.P$24 (24), EPS/OBC.P$23 (23), EPS/OBC.P$24 (24), FAB.P$23 (23), FAB.P$24 (24), MSN_I.P$23 (23), MSN_I.P$24 (24), MSN_II.P$23 (23), MSN_II.P$24 (24), RAB.P$23 (23), RAB.P$24 (24)
SUP_UNREG_2: COM.P$35 (35), COM.P$36 (36), EPS/OBC.P$35 (35), EPS/OBC.P$36 (36), FAB.P$35 (35), FAB.P$36 (36), MSN_I.P$35 (35), MSN_I.P$36 (36), MSN_II.P$35 (35), MSN_II.P$36 (36), RAB.P$35 (35), RAB.P$36 (36), SP2/-Y.3
TEMP1_+X_NEW: FAB.P$28 (28), SP1/+Y.10
TEMP2_-Y_NEW: FAB.P$22 (22), SP4/+X.10
TEMP3_-Z_NEW: FAB.P$34 (34), SP5/-Z.10
TEMP4_+Y_NEW: FAB.P$38 (38), SP3/-X.10
TEMP5_-X_NEW: FAB.P$32 (32), SP2/-Y.10

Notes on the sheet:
Temperature Sensor
Deployment Switches
Solar Panel Connectors
BIRDS-4 BPB

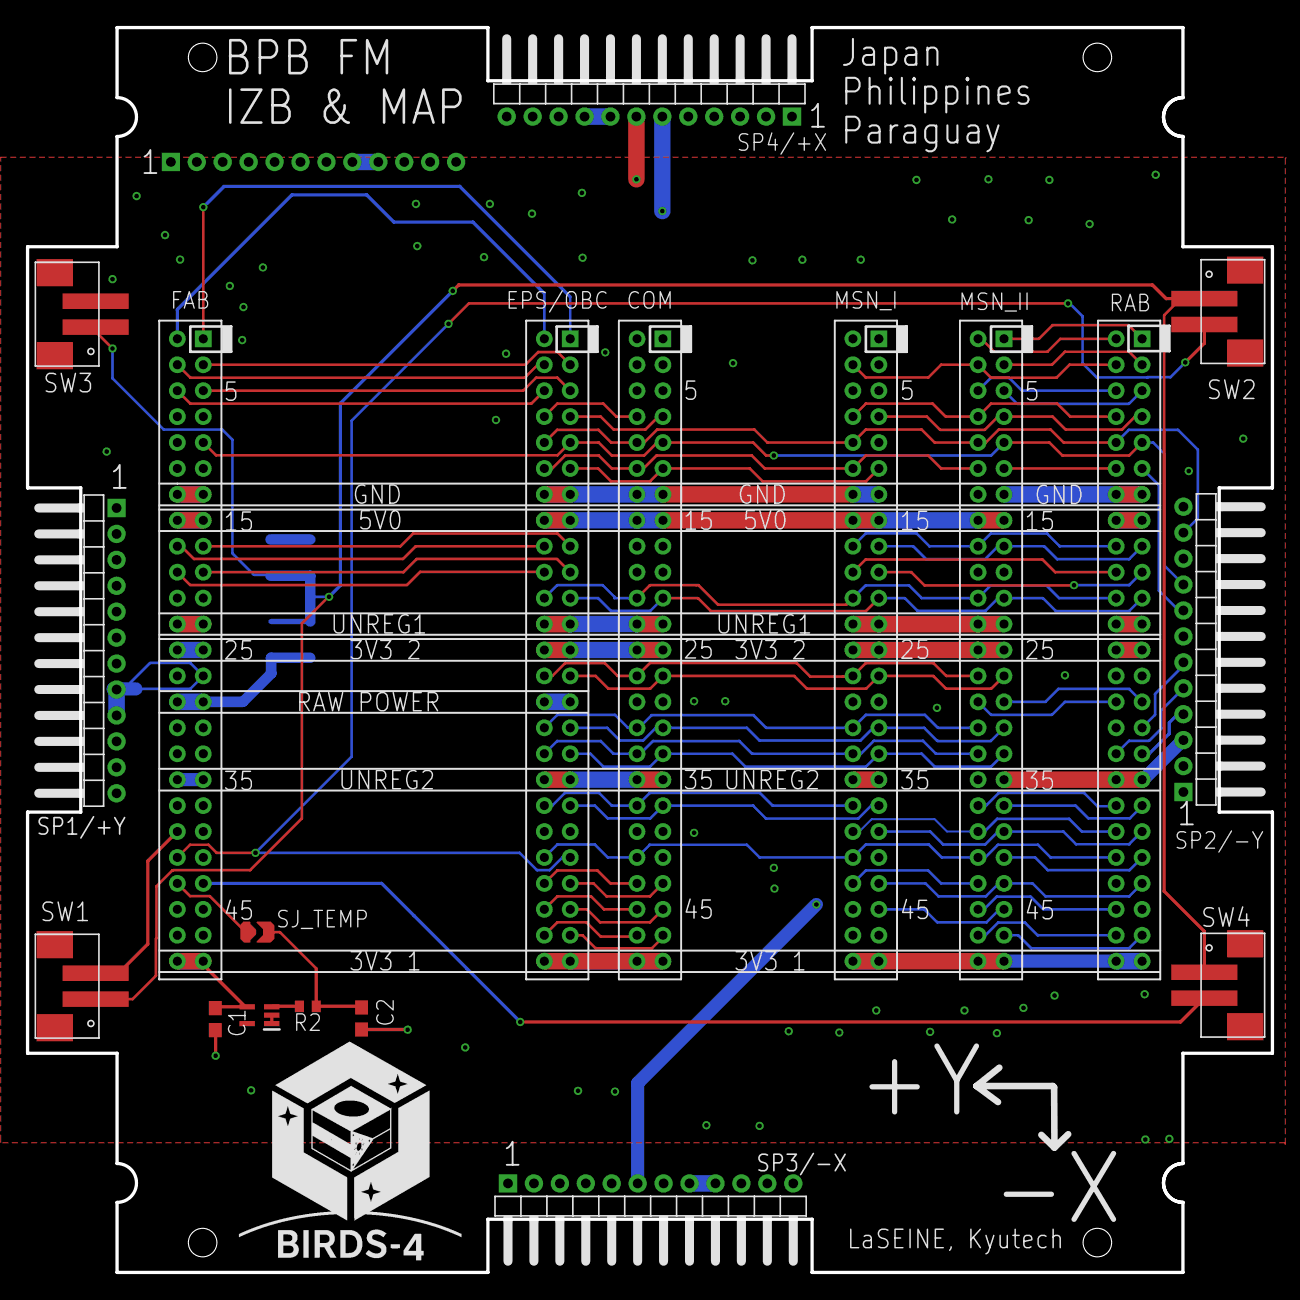
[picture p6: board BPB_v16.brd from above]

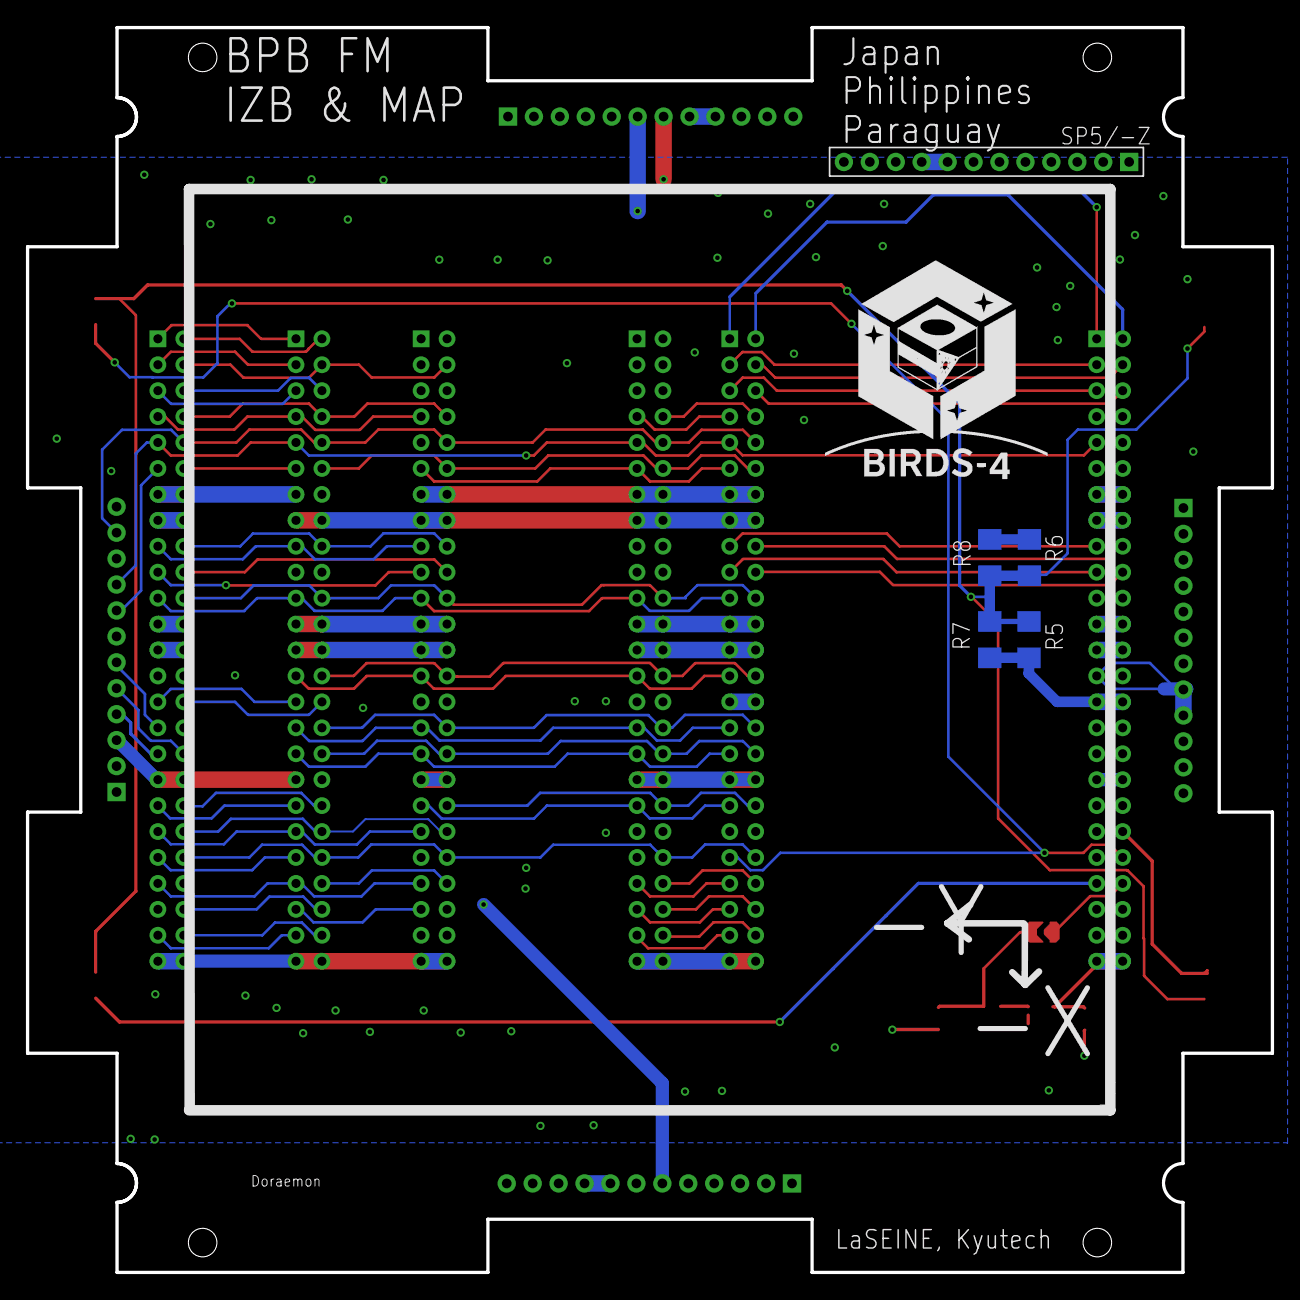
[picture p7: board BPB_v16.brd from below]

Board: 4 copper layers, 96.0 x 96.0 mm, 24 parts (5 on the bottom side), 94 nets.
